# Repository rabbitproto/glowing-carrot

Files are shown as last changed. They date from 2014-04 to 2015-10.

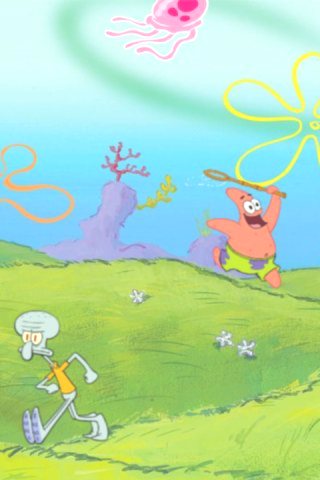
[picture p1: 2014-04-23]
demo_applications/Game Controller/Jellyfish Fields/Jellyfish_Fields/background.jpg

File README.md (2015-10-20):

Rabbit Proto Logo

Attention! Rabbit Proto is now part of Nascent Objects, we are not shipping extruders or machine anymore, but have open sourced all the latest extruder design files so the community can take over and make their own. More information on this post:

<script async src="https://static.medium.com/embed.js"></script><a class="m-story" data-collapsed="true" href="https://medium.com/@AlexandreJais/building-the-future-of-making-265a1de3fc73">Building the future of making</a>

Rabbit Proto
==============

##What##

Rabbit Proto makes plugins that easily integrate into your 3D printer, enabling it to print complex conductive traces within 3D designs.  Your 3D printer can now print interactive prototypes with capacitive and conductive features.

##Who##

Rabbit Proto has been created for designers and makers, by designers and makers - you can now speed up your prototyping and ideation process, going from computer design to interactive prototype with just one click.

##How##

Rabbit Proto is a print head add-on that easily plugs into your 3D printer, enabling it to print complex conductive traces within your 3D design. The project source code, documentation, and example designs are open source and available on GitHub. 

See Rabbit Proto in action on our website : www.rabbitproto.com

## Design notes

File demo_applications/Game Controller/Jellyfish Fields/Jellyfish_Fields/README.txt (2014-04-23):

This code won't work until you have something connected to your serial com port. So connect your Arduino, otherwise the sketch won't play.

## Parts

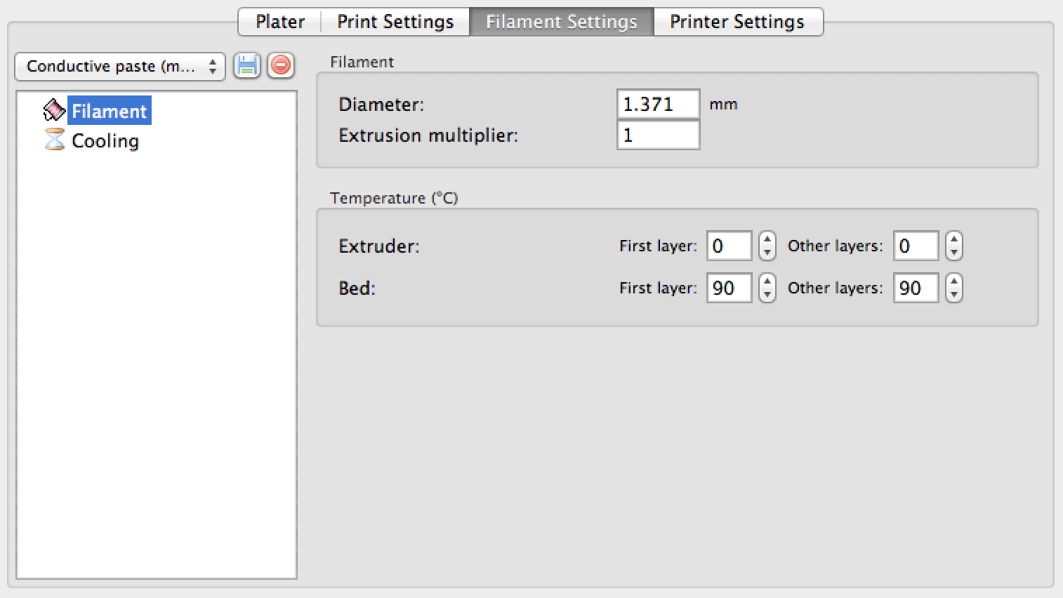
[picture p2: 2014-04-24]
Slicer Settings/Conductive Paste Material Properties.png

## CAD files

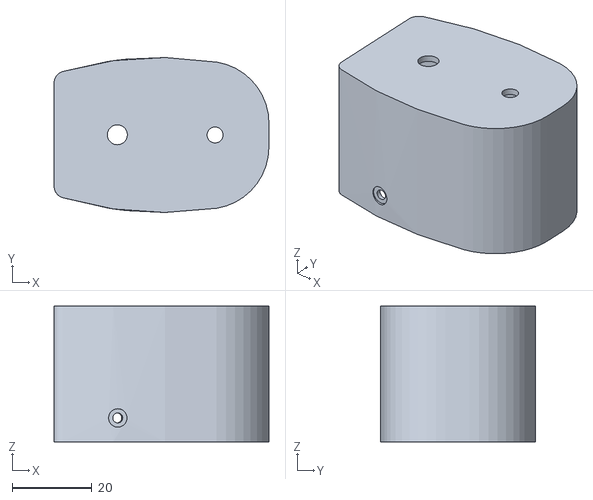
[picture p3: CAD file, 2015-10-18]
extruder_design/Dual Extruder/Extruder Assembly - Top.stl
53.8 x 38.8 x 34.0

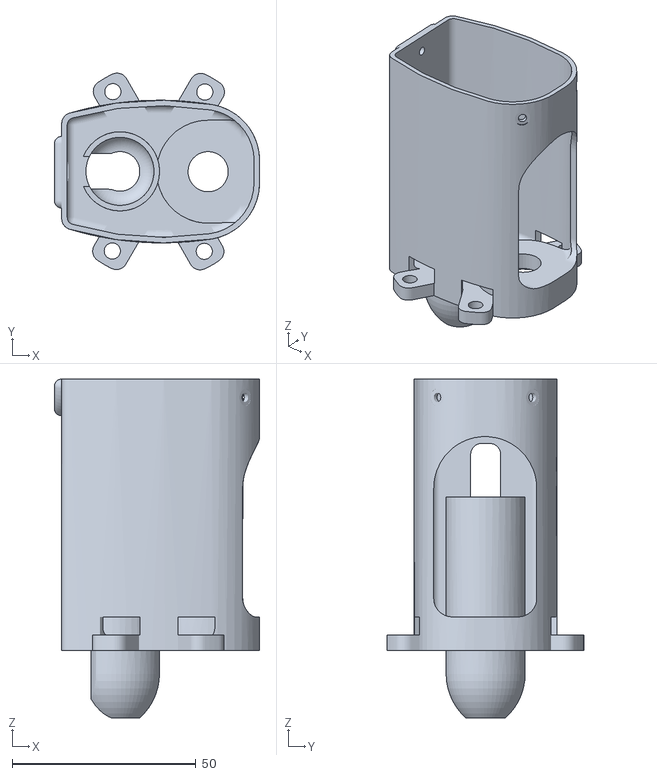
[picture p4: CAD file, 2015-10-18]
extruder_design/Dual Extruder/Extruder Assembly - Bottom.stl
55.8 x 53.5 x 92.2

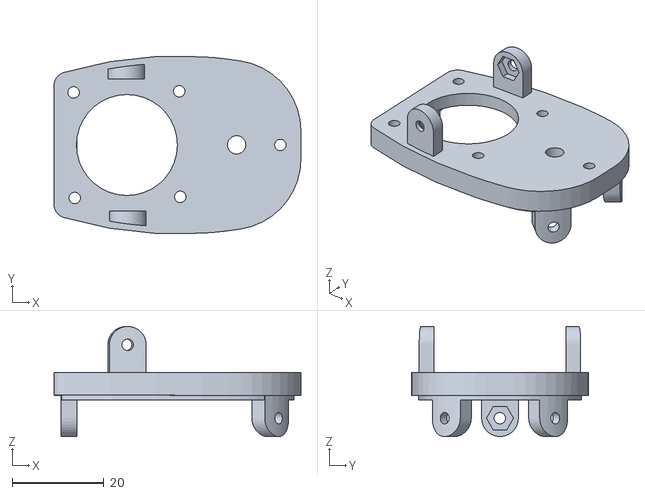
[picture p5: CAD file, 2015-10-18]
extruder_design/Dual Extruder/Extruder Assembly - Middle.stl
53.8 x 38.6 x 24.0

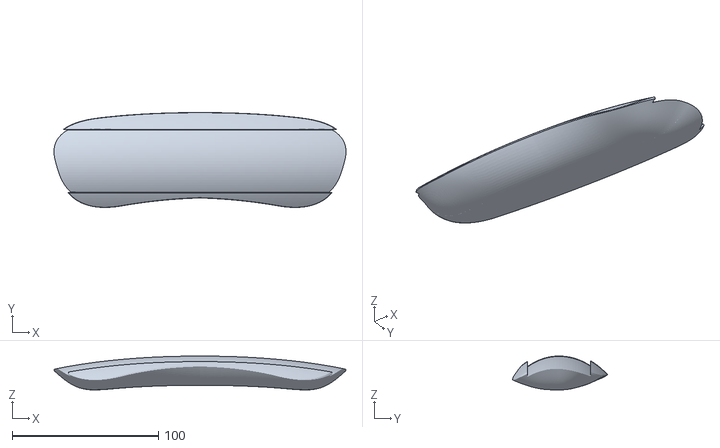
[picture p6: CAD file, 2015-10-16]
demo_applications/backrest_ll_btmcase.stl
199.6 x 64.9 x 23.2

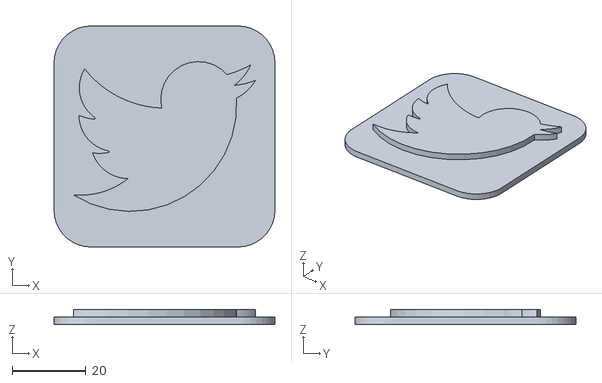
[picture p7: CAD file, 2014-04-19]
demo_applications/Conductive Twitter/Twitter3.stl
60.0 x 60.0 x 4.00

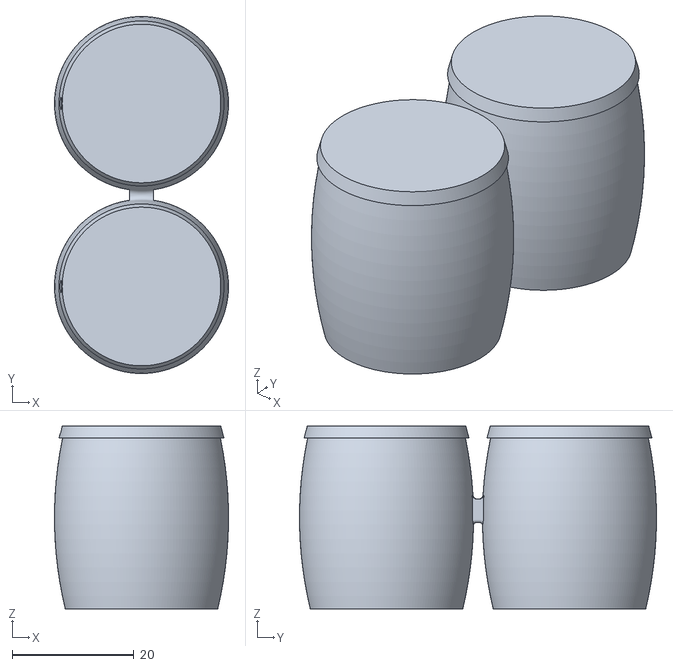
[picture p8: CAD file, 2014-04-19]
demo_applications/Congas/Congas.stl
28.5 x 58.5 x 30.0

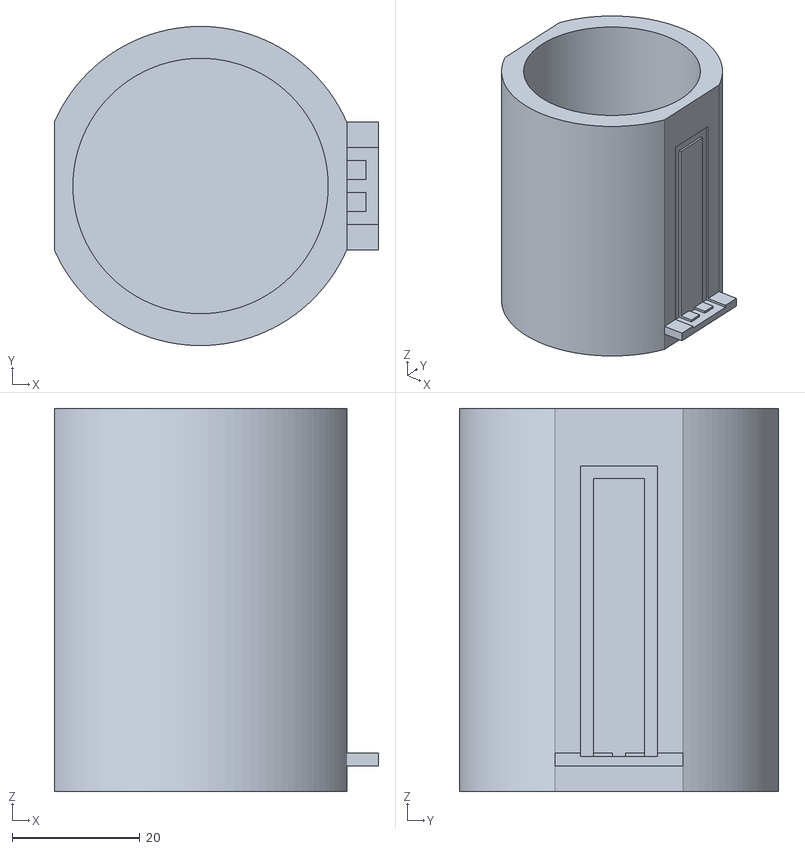
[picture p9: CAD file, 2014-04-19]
demo_applications/Cup measurement/Cup.stl
50.8 x 50.0 x 60.0

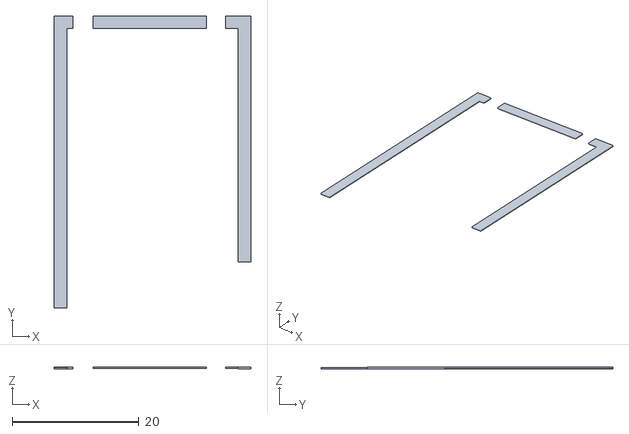
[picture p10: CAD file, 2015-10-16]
demo_applications/Cute octopus/CuteOcto(2).stl
31.0 x 46.0 x 0.301

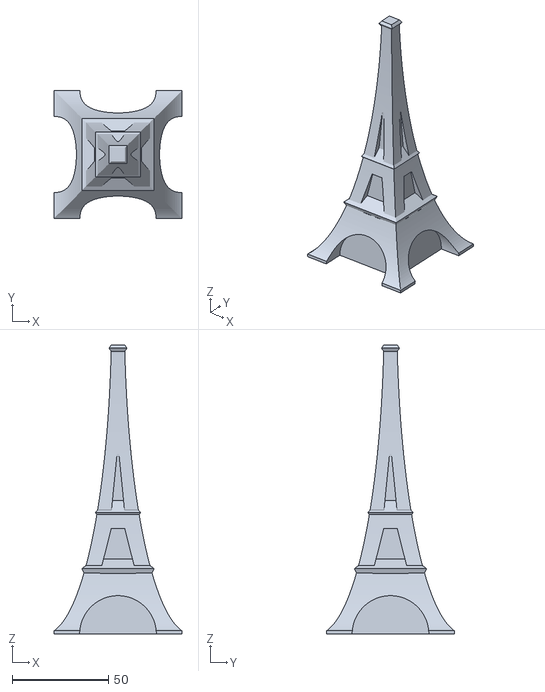
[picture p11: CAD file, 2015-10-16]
demo_applications/Eiffel Tower/Eiffel Tower.stl
66.3 x 66.3 x 150.0

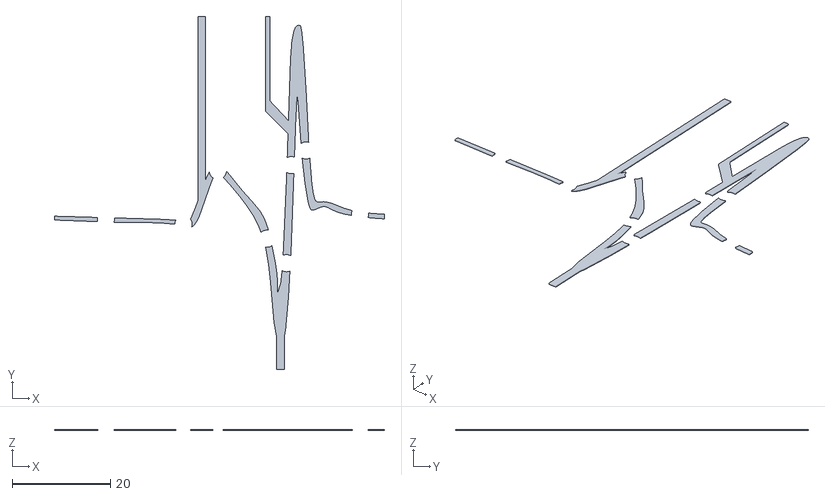
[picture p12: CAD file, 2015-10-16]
demo_applications/EKG light/EKG light V2.stl
67.3 x 72.0 x 0.25

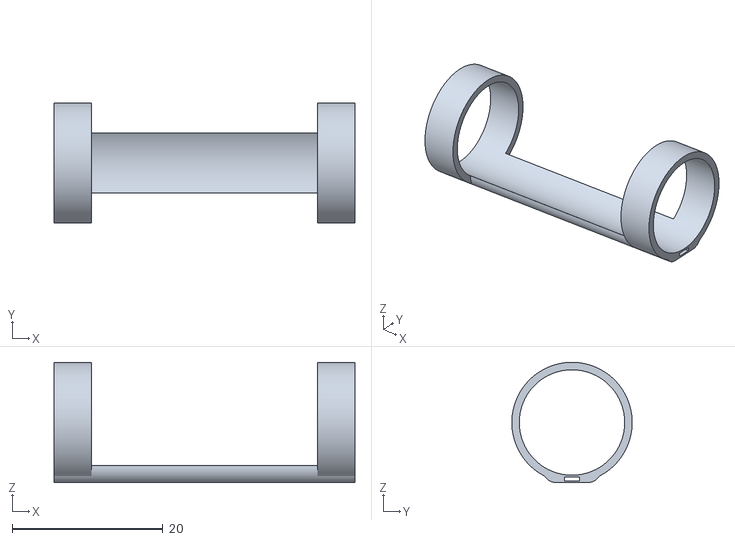
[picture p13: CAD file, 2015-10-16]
demo_applications/Finger Flex/Finger Flex.stl
40.0 x 16.0 x 16.0

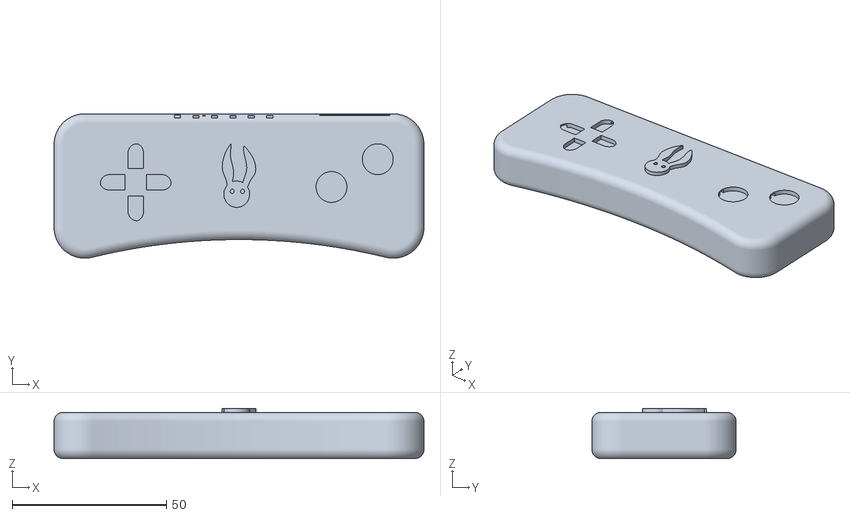
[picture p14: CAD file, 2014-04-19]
demo_applications/Game Controller/CAD/Game Controller.stl
120.0 x 46.8 x 16.3

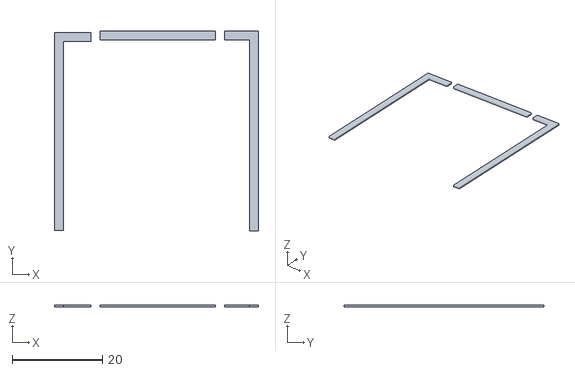
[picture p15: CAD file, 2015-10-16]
demo_applications/Glowing Rabbit 2/Glowing Rabbit 2.stl
45.2 x 44.2 x 0.5

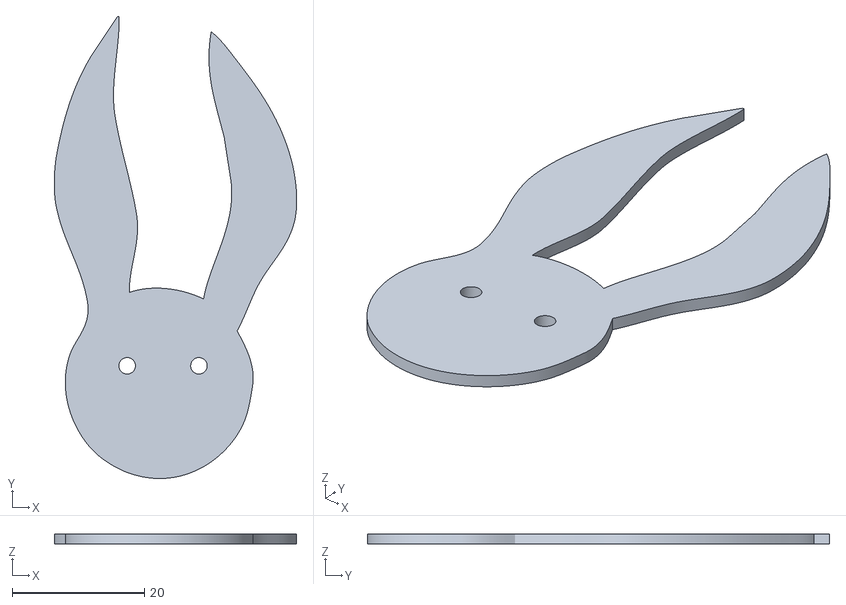
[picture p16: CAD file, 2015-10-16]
demo_applications/Glowing Rabbit 3/Glowing Rabbit.stl
36.7 x 70.0 x 1.50

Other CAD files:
demo_applications/IPhone Stylus/IPhone Stylus v3.stl
demo_applications/IPhone Stylus/Test shapes/Feather Stylus.stl
demo_applications/IPhone Stylus/Testing Session/IPhone Stylus v3.stl
demo_applications/Calibration Shapes/Design4.stl
demo_applications/Calibration Shapes/backrest_ll_topcase.stl
demo_applications/Conductive Twitter/Twitter(2).stl
demo_applications/Conductive Twitter/Twitter.amf
demo_applications/Conductive Twitter/Twitter2(2).stl
demo_applications/Conductive Twitter/Twitter3(2).stl
demo_applications/Conductive Twitter/Twitter3.amf
demo_applications/EKG light/EKG light V2(2).stl
demo_applications/EKG light/EKG light V2.amf
demo_applications/EKG light/EKG light thin(2).stl
demo_applications/EKG light/EKG light thin.amf
demo_applications/EKG light/EKG light(2).stl
demo_applications/EKG light/EKG light.amf
demo_applications/EKG light/EKG light.stl
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

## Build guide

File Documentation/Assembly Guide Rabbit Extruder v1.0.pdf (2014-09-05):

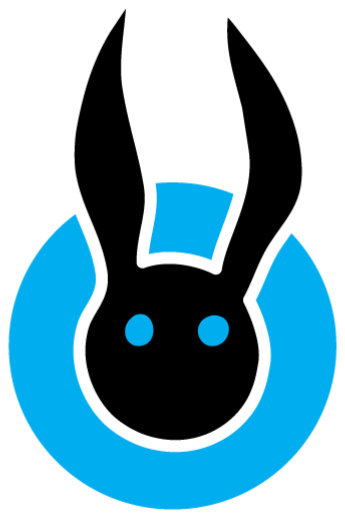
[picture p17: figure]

Please email questions or corrections to info@rabbitproto.com

# Quick guide - Rabbit Proto Extruder

V1.0 Sept 2014

## 1. Material required

Hardware
- Rep Rap 3D printer
- Rabbit Proto – Supper Rabbit PrintHead
- Copper filled silicone RTV (http://www.amazon.com/Permatex-81878-Maximum-Temperature-Silicone/dp/B0002UEOPA) (http://www.amazon.com/Permatex-81878-Maximum-Temperature-Silicone/dp/B0002UEOPA)
- Kapton tape
- Allen Wrench (Metric)
Software
- Repetier Host + Slic3r
- Arduino Software

## 2. Finalize the plastic extruder assembly

From the Rostock Max Assembly guide by SeeMeCNC

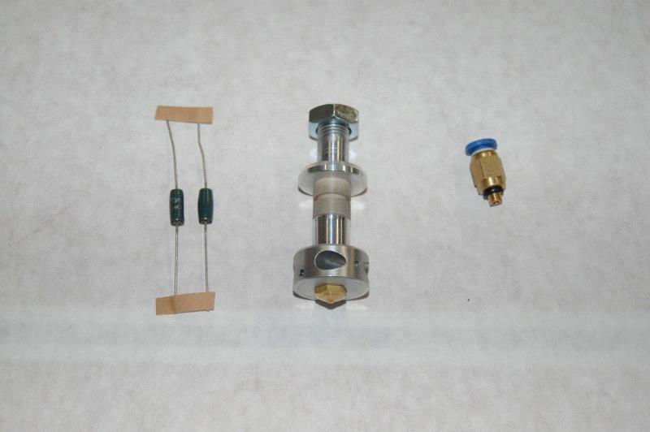
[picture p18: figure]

Hot end components.

The only tasks you need to complete involve installing the heating resistors, the thermistor and the push-fit connector.

The resistors included with the hot end (the green objects in Fig. 15-1) are too small to fit snugly into the bore holes to either side of the hot end. In order to make them bigger, you’ll need to cut a strip of aluminum foil and wrap the resistor. You want the width of the foil strip to be about 1/16” shorter than the length of the resistor body so that it can’t come into contact with the leads on either end of the resistor.

Note that in order to shield the resistor leads from accidental shorts, you should wrap the leads in Kapton tape.

Once you've got the resistors installed in the hot end with a snug fit, cover each end with RTV to glue them into place. We use RTV here because if you have a resistor failure, it can be removed easily, but is very resistant to high temperatures.

Before the RTV cures, install a 3/4” length of PTFE tubing on each of the resistor leads as shown below.

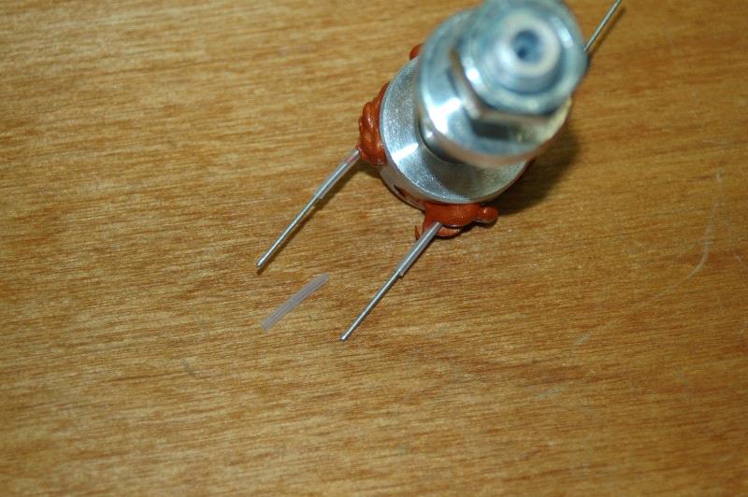
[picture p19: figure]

Insulating the hot end resistor leads.

Once the RTV cures, carefully twist the resistor leads together as shown below. Use a pair of needle nose pliers to help you get a good, tight twist.

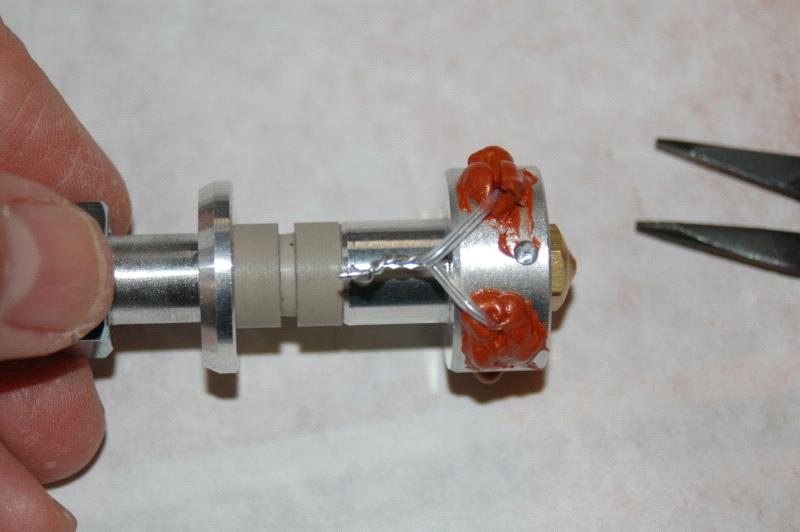
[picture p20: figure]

Resistor leads twisted together

When you're done twisting the leads together, clip about 1/16” to 1/8” off each end to clean up the ends a bit. A crimp connector will go on them and you want the best fit you can get.

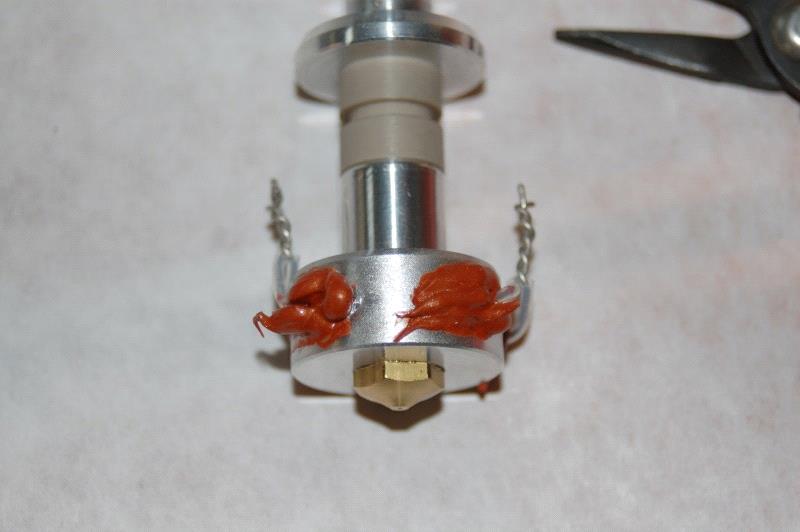
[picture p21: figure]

Resistor leads ready to crimp.

Because of the temperatures reached by the hot end, we can't use solder to attach the power wires to the resistors. Use crimps marked “22-16”. Crimp one connector to each twisted pair of resistor leads as shown below.

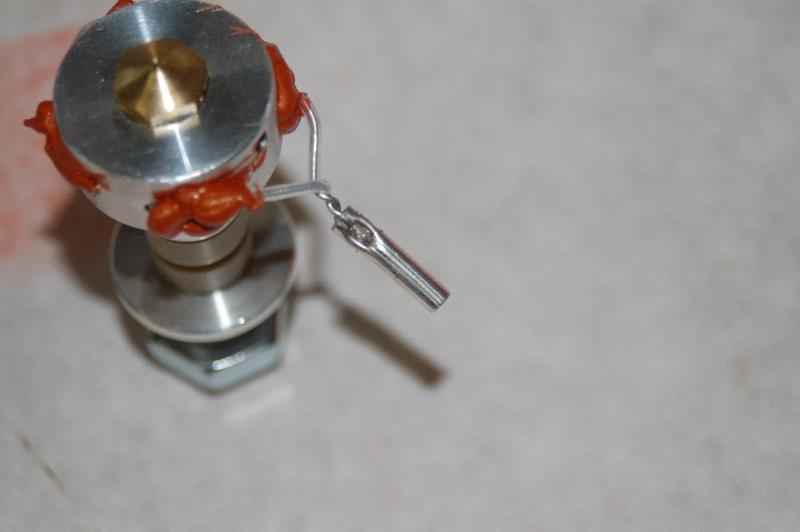
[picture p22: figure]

Crimp on connector in place.

Note that you only want to crimp it in one place.

The lower portion of the hot end is threaded on to a PEEK barrel that acts like a thermal break. In order to keep repeated heating and cooling cycles from loosening the hot end from the PEEK, wrap the seam with a short length of Kapton tape as shown below.

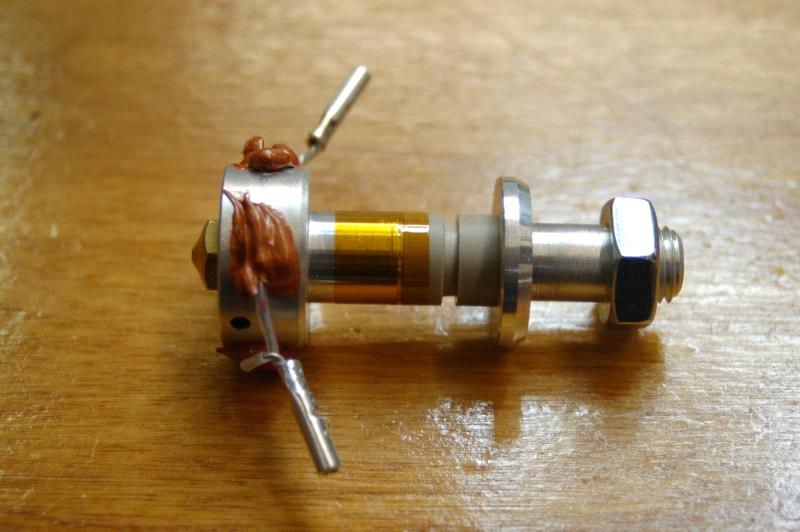
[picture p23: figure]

Kapton wrap on the PEEK barrel.

I prefer to use a quick disconnect connector on my hot-end and I strongly suggest you do the same. In Section 1 I list two different types – the Deans and XT-60 connectors. My preference is the XT-60, but if you've got Deans on hand, they're well suited to the task. I won't show how to attach them – it should be pretty obvious and if not, there's always Google. :) I'm going with the assumption that you like to be able to change out hot-ends and have installed the connectors of your choice.

Attach a 3” or so length of 16ga wire (one black, one red) to the crimped connectors, and wrap them in Kapton tape to insulate them.

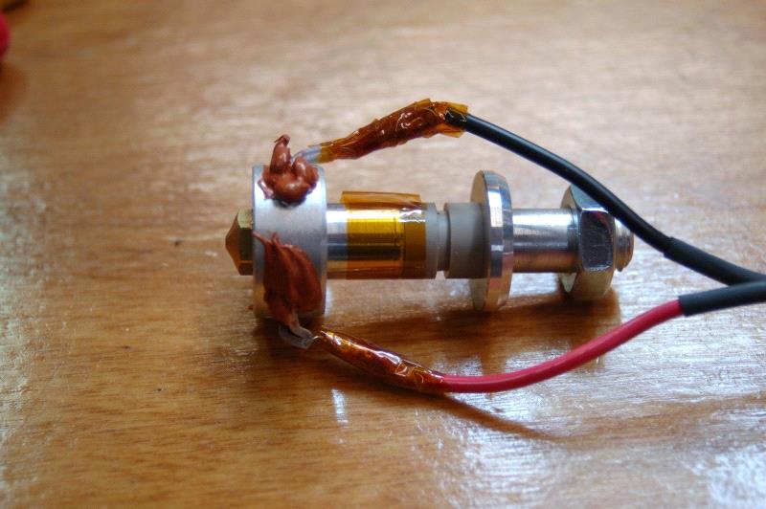
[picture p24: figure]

Attaching the power leads to the hot end.

Now you need to install the thermistor into the hot end. A thermistor is a tiny temperature sensing device that changes resistance as the temperature around it changes. I cannot stress this enough it's a very delicate component! Please handle it very carefully! The glass bead is fragile and the wire can be brittle if soldered and moved too much.

First, cut two 1” lengths of the included PTFE tubing and slide them over the thermistor leads as shown:

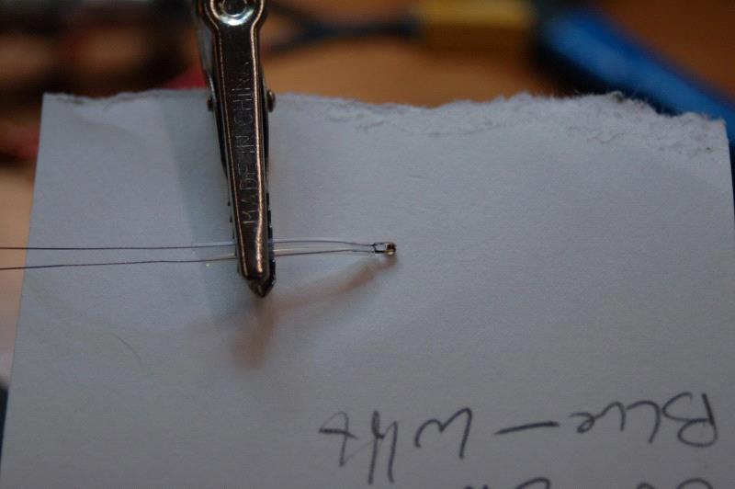
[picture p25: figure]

Insulating the thermistor leads.

Just like the resistor wiring, I recommend you use a quick disconnect connector. For the thermistor, I recommend using a JST connector. You can cut a 2” long section from the wiring supplied for doing the stepper motor extension for this purpose. Thermistors have no polarity, so it doesn't matter how you attach the JST connectors.

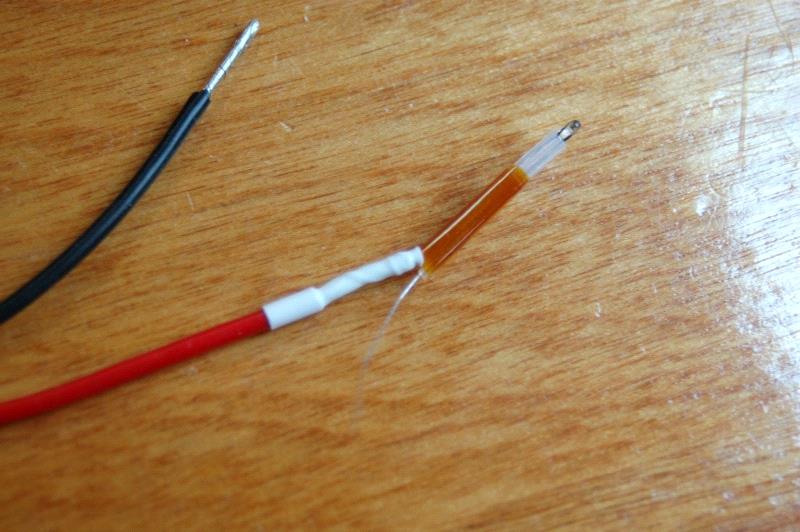
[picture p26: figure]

Attaching leads to the thermistor.

Now you can solder your leads to the thermistor. I recommend covering the solder joint with heat shrink tubing. The thermistor wires won't get hot enough to affect it. You'll also see that I taped the leads together with Kapton tape. This is done to give it a bit more protection.

Be careful when you're soldering this up. The thermistor leads are very brittle and can break easily once soldered.

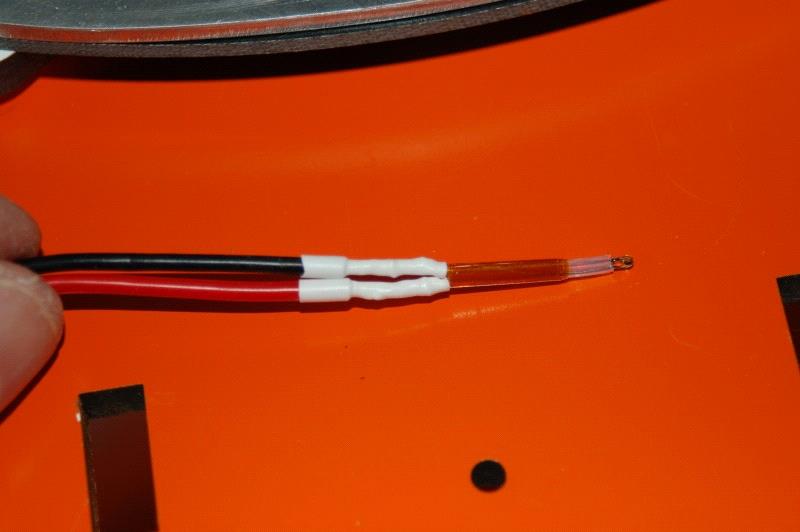
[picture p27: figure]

Thermistor ready to install.

Once you've got the leads added, I strongly suggest that you use Kapton tape or more heat shrink to bind the two leads together at the joint – this will help prevent flex that could cause the thermistor lead solder joint to fail. The thermistor is installed in the hot end at the location shown in Fig. 15-11.

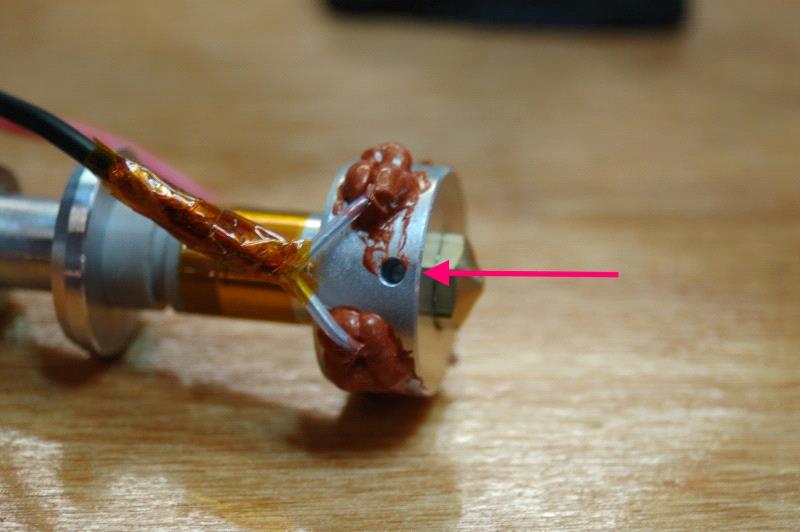
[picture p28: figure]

Thermistor installation location.

In order to “glue” the thermistor into place, you'll need to coat the sides of the thermistor bead with a small amount of RTV as shown in Fig. 15-12.

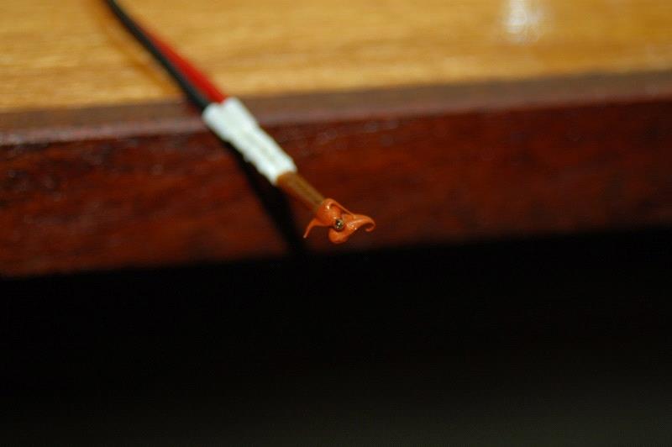
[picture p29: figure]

RTV applied to the thermistor sides.

The idea here is to leave the tip of the glass bead exposed. This will allow it to come into unobstructed contact with the thermistor port on the hot end.

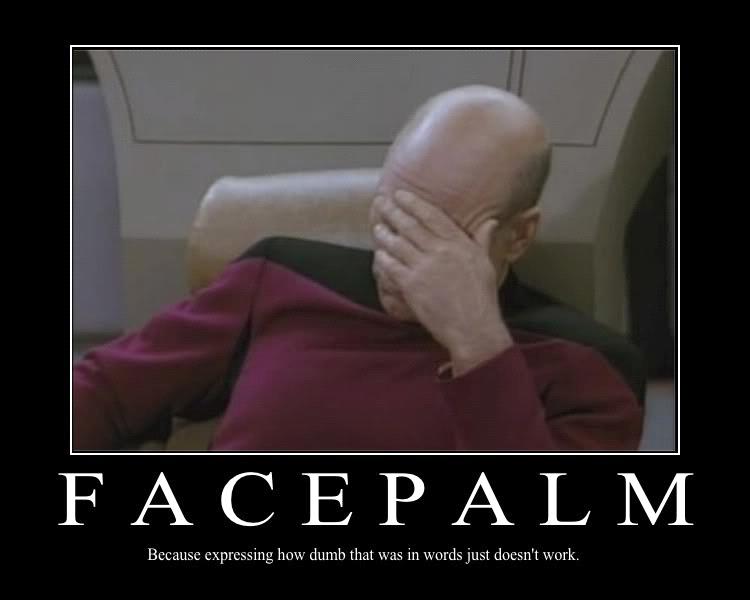
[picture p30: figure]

D'OH!

Wait, you just broke the wires on your thermistor, didn't you? Oh. You didn't? Well I just did.

So instead of doing the technical writing equivalent of sweeping the bits of broken ceramic under the couch with your foot while smiling and telling your mother you have no idea where her prize vase is, I'm going to show you photos of the thermistor as I actually installed it.

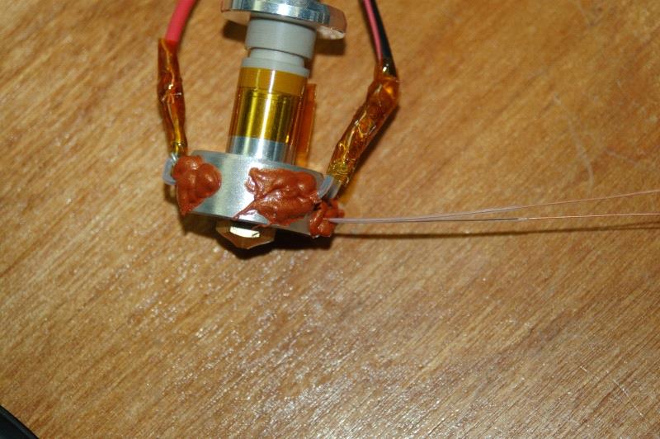
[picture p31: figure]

Magically repaired (and slightly different) thermistor installed in the hot end.

Please give the RTV time to fully cure before you move on to the next steps.

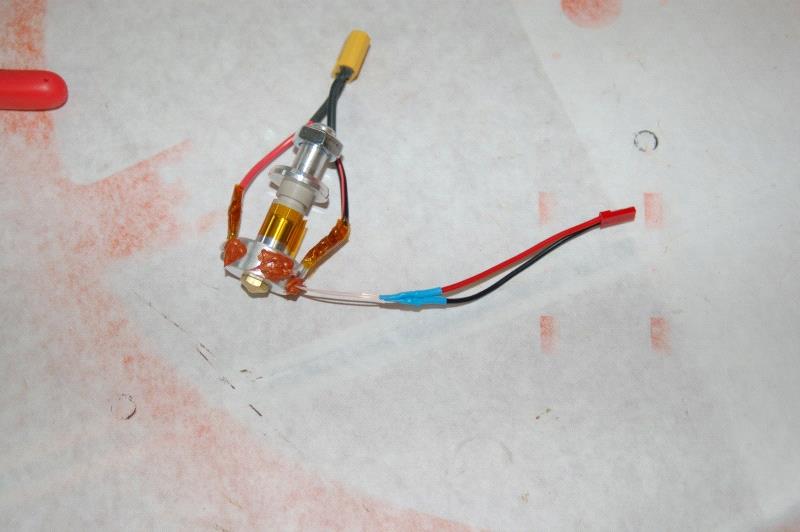
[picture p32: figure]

Magic thermistor with JST connector in place.

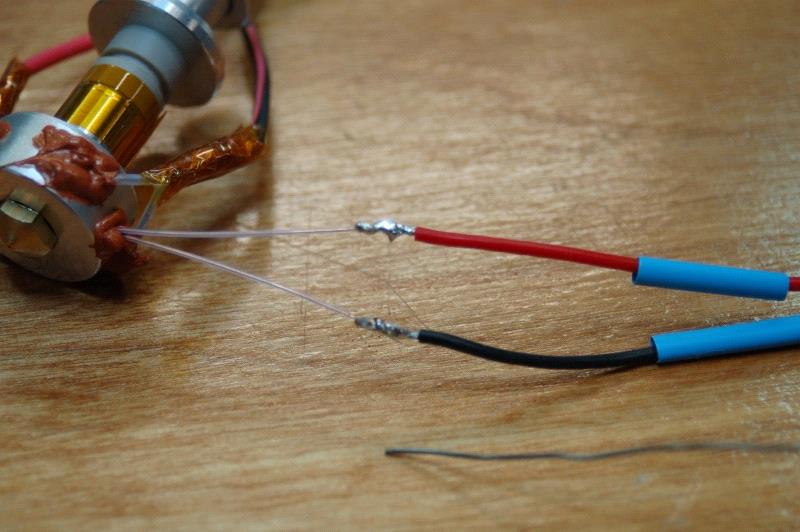
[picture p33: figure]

Magic thermistor getting JST connector.

## 3. Attach the extruder to your 3D printer

a. Design and print an adapter (if needed)

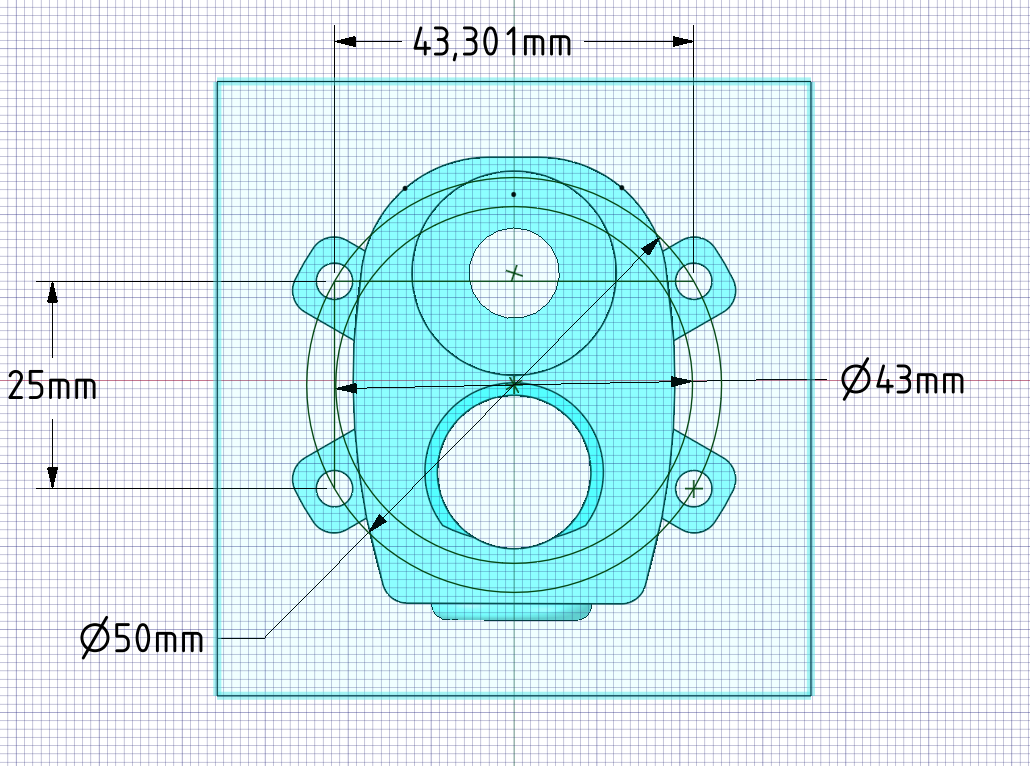
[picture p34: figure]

Rabbit Proto’s footprint.
If you own a Mendel Prusa or a Rostock, there is a high chance you will be able to attach the RP extruder directly to your machine. Otherwise you should be able to print a carriage adapter that can hold the extruder.
b. Optional – Bowden extruder assembly
If you don’t have a Bowden-compatible extrusion system, we have included an Ezstruder system from SeeMeCnc (http://seemecnc.com/products/ezstruder-cold-end-kit). Assembly should be straightforward but you’ll find documentation on their website (or look at this video and ignore the hot-end assembly part). https://www.youtube.com/watch?v=2bmbvPiY7qM#t=191
c. Attach to the printer or your homemade adapter using screw and self-locking nuts preferably
d. Connect the second extruder stepper motor on your board. If your printer is compatible with dual extrusion, you should have an available port for the conductive paste extruder stepper motor.

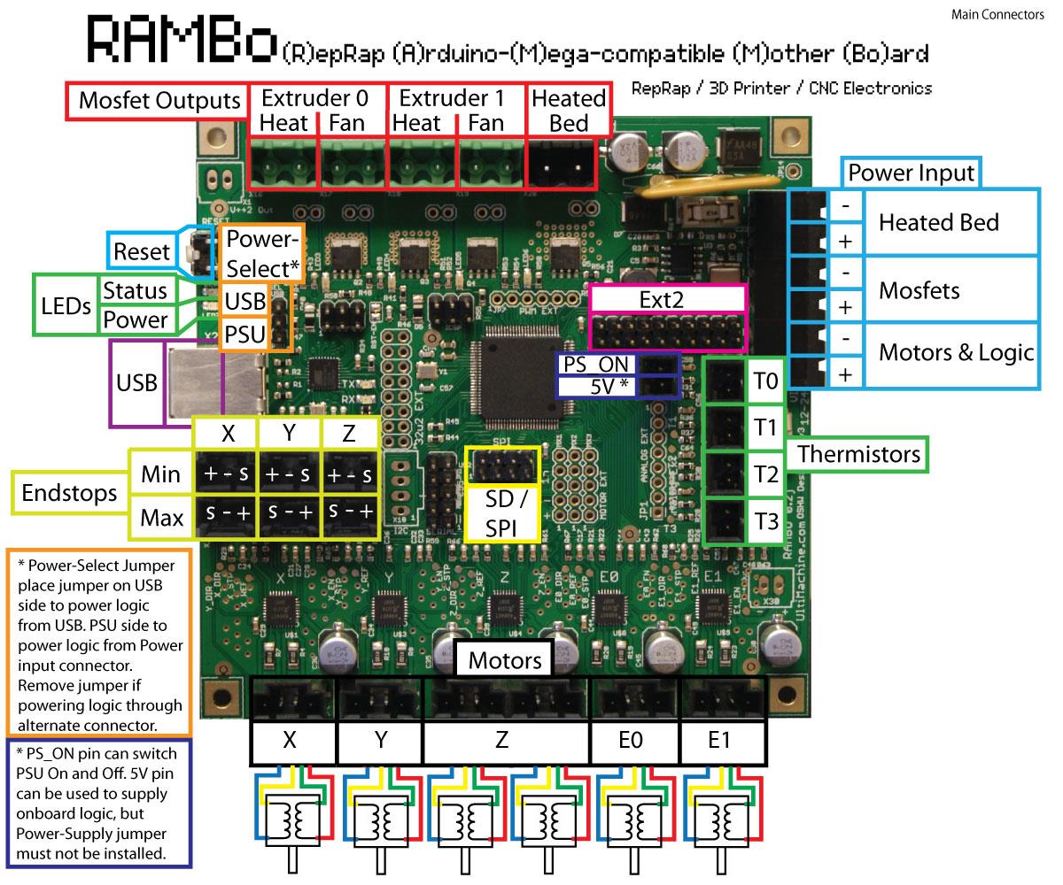
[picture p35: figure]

On the Rambo Board use the port noted E1.

## 4. Modify your printer’s firmware

In order to be able to use your second extruder, you need to modify the configuration file of the firmware of your machine. The amount of modification is in general extremely small especially if the settings of your printer can be modified with the EEPROM. You can find a copy of a modified Repetier Firmware for Rostock Max on our github at https://github.com/rabbitproto/glowing-carrot/. The three most important steps to take:
- Set up two extruders
- Allow cold extrusion (so that your second extruder can work even without any thermistor checking the temperature).
- Tune up the number of steps per mm for the second extruder (1100 steps/mm).
- If you end-up using the Ez-struder, you will also need to change the number of steps per mm.

## 5. Configuration in Repetier Host/Slic3r

Tuned Slic3r parameters:
Parameters | Values
Layer Height | 0.2mm
First Layer Height | 0.35mm
Minimum Perimeters | 2
Fill Density | 1
Fill Pattern | Rectilinear
Top/Bottom Fill Pattern | Rectilinear
Infill Every # Layers | 1
Solid Infill Every # Layers | 1
Fill Angle | 0
Perimeter Speed | 60mm/s
Small Perimeter Speed | 10mm/s
External Perimeter Speed | 70%
Infill Speed | 60mm/s
Solid Infill Speed | 60mm/s
Top Solid Infill Speed | 60mm/s
Support Material Speed | 60mm/s
Bridges Speed | 60mm/s
Gap Speed | 60mm/s
Non Printing Speed | 130mm/s
First Layer Speed | 30%
Skirt Loops | 2
Skirt Distance from Objects | 6mm
Skirt Height | 1 Layer Height
Support Material Pattern | Rectilinear
Support Material Pattern Spacing | 2.5mm
Support Material Pattern Angle | 0
Default Extrusion Width | 0.4mm
First Layer Extrusion Width | 300%
Plastic Filament Diameter | 1.75 mm (please check for your own
| filament)
Plastic Extrusion Multiplier | 1
Plastic Extrusion Nozzle Temperature | 230°C
Plastic Extrusion Print-bed Temperature | 55
Syringe Filament Diameter | 7.358491
Syringe Extrusion Multiplier | 4
Syringe Extrusion Nozzle Temperature | 0
Syringe Extrusion Print-bed Temperature | 0
Print-bed Size | Depending on your printer
Printer Center | Depending on your printer
Number of Extruders | 2

Z-offset | 0
Plastic Extruder Retraction Length | 0.5mm
Plastic Extruder Retraction Speed | 6mm/s
Tool Change Retraction Length for Plastics | 0.5mm
Syringe Extruder X-offset | 1.1mm
Syringe Extruder Y-offset | -24.6mm
Syringe Extruder Retraction Length | 0.001mm
Syringe Extruder Retraction Speed | 1mm/s
Extra Extrusion on Restart for Syringe | 0.01mm
Tool Change Retraction Length for Syringe | 0

Please fine tune the offsets and the extrusion multipliers as there could be some fine modifications needed after a few prints.

## 6. Generating a CAD file

In order to generate a proper CAD file for printing with the Rabbit Extruder, you can use any standard CAD solution as long as you are able to generate multiple components that will be outputted as STL files. One will contain the plastic, the other one the conductive traces. You will want to have wells pre-formed into your plastic parts to hold the conductive traces. You can also add cavities for holding electronic components that you can pick and place during or after the print:

General requirements for design:
Features | Dimensions
Conductive traces | for cross-section 1.20x0.4mm
Plastic wells to contain conductive
traces

for cross-section 2.0x0.6mm

Cavities to hold SMT LEDs | 4.3x1.2x1.2mm
Cavities to hold regular resistors | 7.6x2.8x3.5mm
Cavities to hold 3 parallel male pin
headers

9.5x3.5x3mm

Cavities to hold 3 parallel female pin
headers

9.2x3.2x8.9mm

Cavities to hold 2025 button batteries Dia: 21mm thickness 5.8mm

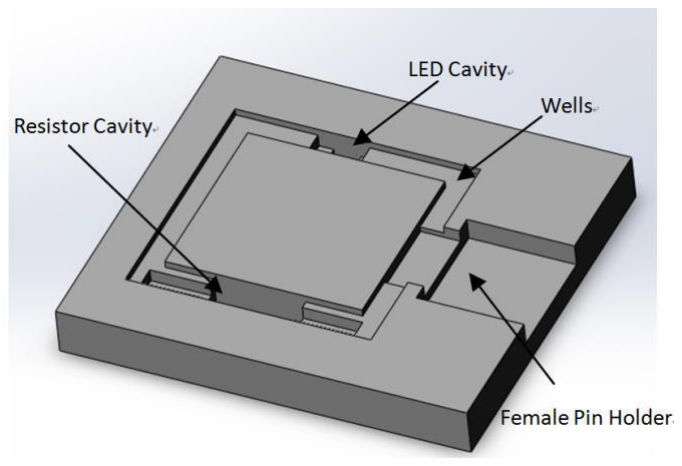
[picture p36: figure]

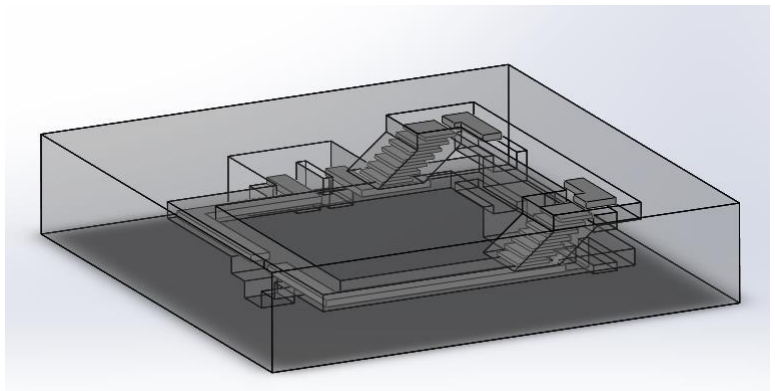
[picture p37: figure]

## 7. Printing using Repetier Host

Slic3r can output gcode for a multi-material printer, which can then be read inside repetier host. You can find more details on how to generate proper gcode at http://manual.slic3r.org/expert-mode/multiple-extruders.

## 8. Uploading your designs

Please share your designs with the Rabbit Proto community! A current repository of designs is available on our github, at https://github.com/rabbitproto/glowing-carrot/tree/master/demo_applications, (https://github.com/rabbitproto/glowing-carrot/tree/master/demo_applications) and our twitter handle is @rabbitproto.

Please email questions or corrections to info@rabbitproto.com

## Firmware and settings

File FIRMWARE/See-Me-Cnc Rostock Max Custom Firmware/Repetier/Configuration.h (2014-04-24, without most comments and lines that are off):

#define CONFIGURATION_H
#define NUM_EXTRUDER 2
#define MOTHERBOARD 301
#include "pins.h"
#define DRIVE_SYSTEM 3
#if DRIVE_SYSTEM==3
    #define DELTA_DRIVE_TYPE 0
    #if DELTA_DRIVE_TYPE == 0
      #define BELT_PITCH 2
      #define PULLEY_TEETH 20
      #define PULLEY_CIRCUMFERENCE (BELT_PITCH * PULLEY_TEETH)
    #elif DELTA_DRIVE_TYPE == 1
      #define PULLEY_DIAMETER 10
      #define PULLEY_CIRCUMFERENCE (PULLEY_DIAMETER * 3.1415927)
    #endif
    #define STEPS_PER_ROTATION 200
    #define MICRO_STEPS 16
    #define MAX_DELTA_SEGMENTS_PER_LINE 30
    #define AXIS_STEPS_PER_MM ((float)(MICRO_STEPS * STEPS_PER_ROTATION) / PULLEY_CIRCUMFERENCE)
    #define XAXIS_STEPS_PER_MM AXIS_STEPS_PER_MM
    #define YAXIS_STEPS_PER_MM AXIS_STEPS_PER_MM
    #define ZAXIS_STEPS_PER_MM AXIS_STEPS_PER_MM
#else
    #define XAXIS_STEPS_PER_MM 80.000
    #define YAXIS_STEPS_PER_MM 80.000
    #define ZAXIS_STEPS_PER_MM 80.000
#endif
#define EXTRUDER_FAN_COOL_TEMP 40
#define EXT0_X_OFFSET 0
#define EXT0_Y_OFFSET 0
#define EXT0_STEPS_PER_MM 92.000 //steves extruder    set to 92 for ezstruder
#define EXT0_TEMPSENSOR_TYPE 8
#define EXT0_TEMPSENSOR_PIN TEMP_0_PIN
#define EXT0_HEATER_PIN HEATER_0_PIN
#define EXT0_STEP_PIN E0_STEP_PIN
#define EXT0_DIR_PIN E0_DIR_PIN
#define EXT0_INVERSE true
#define EXT0_ENABLE_PIN E0_ENABLE_PIN
#define EXT0_ENABLE_ON false
#define EXT0_MAX_FEEDRATE 40
#define EXT0_MAX_START_FEEDRATE 10
#define EXT0_MAX_ACCELERATION 3500
#define EXT0_HEAT_MANAGER 1
#define EXT0_WATCHPERIOD 1
#define EXT0_PID_INTEGRAL_DRIVE_MAX 205
#define EXT0_PID_INTEGRAL_DRIVE_MIN 60
#define EXT0_PID_P   11.63
#define EXT0_PID_I   0.43
#define EXT0_PID_D 78.65
#define EXT0_PID_MAX 255
#define EXT0_ADVANCE_K 0.0f
#define EXT0_ADVANCE_L 0.0f
#define EXT0_WAIT_RETRACT_TEMP 		150
#define EXT0_WAIT_RETRACT_UNITS 	0
#define EXT0_SELECT_COMMANDS "M120 S5 P5\nM117 Extruder 1"
#define EXT0_DESELECT_COMMANDS ""
#define EXT0_EXTRUDER_COOLER_PIN 7
#define EXT0_EXTRUDER_COOLER_SPEED 255
#define EXT1_X_OFFSET 0
#define EXT1_Y_OFFSET 0
#define EXT1_STEPS_PER_MM 373
#define EXT1_TEMPSENSOR_TYPE 0
#define EXT1_TEMPSENSOR_PIN TEMP_2_PIN
#define EXT1_HEATER_PIN HEATER_2_PIN
#define EXT1_STEP_PIN E1_STEP_PIN
#define EXT1_DIR_PIN E1_DIR_PIN
#define EXT1_INVERSE false
#define EXT1_ENABLE_PIN E1_ENABLE_PIN
#define EXT1_ENABLE_ON false
#define EXT1_MAX_FEEDRATE 25
#define EXT1_MAX_START_FEEDRATE 12
#define EXT1_MAX_ACCELERATION 10000
#define EXT1_HEAT_MANAGER 1
#define EXT1_WATCHPERIOD 1
#define EXT1_PID_INTEGRAL_DRIVE_MAX 130
#define EXT1_PID_INTEGRAL_DRIVE_MIN 60
#define EXT1_PID_P   24
#define EXT1_PID_I   0.88
#define EXT1_PID_D 200
#define EXT1_PID_MAX 255
#define EXT1_ADVANCE_K 0.0f
#define EXT1_ADVANCE_L 0.0f
#define EXT1_WAIT_RETRACT_TEMP 	150
#define EXT1_WAIT_RETRACT_UNITS	40
#define EXT1_SELECT_COMMANDS "M120 S5 P15\nM117 Extruder 2"
#define EXT1_DESELECT_COMMANDS ""
#define EXT1_EXTRUDER_COOLER_PIN -1
#define EXT1_EXTRUDER_COOLER_SPEED 255
#define RETRACT_DURING_HEATUP true
#define PID_CONTROL_RANGE 15
#define SKIP_M109_IF_WITHIN 2
#define SCALE_PID_TO_MAX 0
#define NUM_TEMPS_USERTHERMISTOR0 28
#define USER_THERMISTORTABLE0  {\
  {1*4,864*8},{21*4,300*8},{25*4,290*8},{29*4,280*8},{33*4,270*8},{39*4,260*8},{46*4,250*8},{54*4,240*8},{64*4,230*8},{75*4,220*8},\
  {90*4,210*8},{107*4,200*8},{128*4,190*8},{154*4,180*8},{184*4,170*8},{221*4,160*8},{265*4,150*8},{316*4,140*8},{375*4,130*8},\
  {441*4,120*8},{513*4,110*8},{588*4,100*8},{734*4,80*8},{856*4,60*8},{938*4,40*8},{986*4,20*8},{1008*4,0*8},{1018*4,-20*8}	}
#define NUM_TEMPS_USERTHERMISTOR1 0
#define USER_THERMISTORTABLE1  {}
#define NUM_TEMPS_USERTHERMISTOR2 0
#define USER_THERMISTORTABLE2  {}
#define GENERIC_THERM1_R0 100000
#define GENERIC_THERM1_T0 25
#define GENERIC_THERM1_BETA 4450
#define GENERIC_THERM1_MIN_TEMP -20
#define GENERIC_THERM1_MAX_TEMP 300
#define GENERIC_THERM1_R1 0
#define GENERIC_THERM1_R2 4700
#define GENERIC_THERM2_R0 1042.7
#define GENERIC_THERM2_T0 170
#define GENERIC_THERM2_BETA 4036
#define GENERIC_THERM2_MIN_TEMP -20
#define GENERIC_THERM2_MAX_TEMP 300
#define GENERIC_THERM2_R1 0
#define GENERIC_THERM2_R2 4700
#define GENERIC_THERM3_R0 1042.7
#define GENERIC_THERM3_T0 170
#define GENERIC_THERM3_BETA 4036
#define GENERIC_THERM3_MIN_TEMP -20
#define GENERIC_THERM3_MAX_TEMP 300
#define GENERIC_THERM3_R1 0
#define GENERIC_THERM3_R2 4700
#define GENERIC_THERM_VREF 5
#define GENERIC_THERM_NUM_ENTRIES 28
#define HAVE_HEATED_BED true
#define HEATED_BED_MAX_TEMP 115
#define SKIP_M190_IF_WITHIN 5
#define HEATED_BED_SENSOR_TYPE 8
#define HEATED_BED_SENSOR_PIN TEMP_BED_PIN  //CHANGE FROM TEMP_1_PIN TO TEMP_BED_PIN FOR RAMBo
#define HEATED_BED_HEATER_PIN HEATER_BED_PIN   //CHANGE FROM HEATER_1_PIN TO TEMP_BED_PIN FOR RAMBo
#define HEATED_BED_SET_INTERVAL 5000
#define HEATED_BED_HEAT_MANAGER 1
#define HEATED_BED_PID_INTEGRAL_DRIVE_MAX 255
#define HEATED_BED_PID_INTEGRAL_DRIVE_MIN 80
#define HEATED_BED_PID_PGAIN   15.0
#define HEATED_BED_PID_IGAIN   0.9
#define HEATED_BED_PID_DGAIN 40.0
#define HEATED_BED_PID_MAX 230
#define TEMP_PID true
#define MINTEMP 5
#define MAXTEMP 250
#define MIN_DEFECT_TEMPERATURE -10
#define MAX_DEFECT_TEMPERATURE 300
#define ANALOG_REF ANALOG_REF_AVCC
#define ENDSTOP_PULLUP_X_MIN true
#define ENDSTOP_PULLUP_Y_MIN true
#define ENDSTOP_PULLUP_Z_MIN true
#define ENDSTOP_PULLUP_X_MAX true
#define ENDSTOP_PULLUP_Y_MAX true
#define ENDSTOP_PULLUP_Z_MAX true
#define ENDSTOP_X_MIN_INVERTING true
#define ENDSTOP_Y_MIN_INVERTING true
#define ENDSTOP_Z_MIN_INVERTING true
#define ENDSTOP_X_MAX_INVERTING false
#define ENDSTOP_Y_MAX_INVERTING false
#define ENDSTOP_Z_MAX_INVERTING false
#define MIN_HARDWARE_ENDSTOP_X false
#define MIN_HARDWARE_ENDSTOP_Y false
#define MIN_HARDWARE_ENDSTOP_Z false
#define MAX_HARDWARE_ENDSTOP_X true
#define MAX_HARDWARE_ENDSTOP_Y true
#define MAX_HARDWARE_ENDSTOP_Z true
#define X_ENABLE_ON 0
#define Y_ENABLE_ON 0
#define Z_ENABLE_ON 0
#define DISABLE_X false
#define DISABLE_Y false
#define DISABLE_Z false
#define DISABLE_E false
#define INVERT_X_DIR false
#define INVERT_Y_DIR false
#define INVERT_Z_DIR false
#define X_HOME_DIR 1
#define Y_HOME_DIR 1
#define Z_HOME_DIR 1
#define max_software_endstop_r true
#define min_software_endstop_x false
#define min_software_endstop_y false
#define min_software_endstop_z false
#define max_software_endstop_x true
#define max_software_endstop_y true
#define max_software_endstop_z true
#define ENDSTOP_X_BACK_MOVE 10
#define ENDSTOP_Y_BACK_MOVE 10
#define ENDSTOP_Z_BACK_MOVE 10
#define ENDSTOP_X_RETEST_REDUCTION_FACTOR 4
#define ENDSTOP_Y_RETEST_REDUCTION_FACTOR 4
#define ENDSTOP_Z_RETEST_REDUCTION_FACTOR 4
#define ENDSTOP_X_BACK_ON_HOME 5
#define ENDSTOP_Y_BACK_ON_HOME 5
#define ENDSTOP_Z_BACK_ON_HOME 5
#define ALWAYS_CHECK_ENDSTOPS true
#define X_MAX_LENGTH 360.8
#define Y_MAX_LENGTH 360.8
#define Z_MAX_LENGTH 360.8
#define X_MIN_POS 0
#define Y_MIN_POS 0
#define Z_MIN_POS 0
#define MICROSTEP_MODES {16,16,16,16,16} // [1,2,4,8,16]
#define MOTOR_CURRENT {175,175,175,225,100} // Values 0-255 (RAMBO 135 = ~0.75A, 185 = ~1A)
#if DRIVE_SYSTEM==3
#define DELTA_DIAGONAL_ROD 269.0 // mm
#define DELTA_SEGMENTS_PER_SECOND_PRINT 200 // Move accurate setting for print moves
#define DELTA_SEGMENTS_PER_SECOND_MOVE 70 // Less accurate setting for other moves
#define END_EFFECTOR_HORIZONTAL_OFFSET 33
#define CARRIAGE_HORIZONTAL_OFFSET 35
#define PRINTER_RADIUS 198.25
#define DELTA_RADIUS (PRINTER_RADIUS-END_EFFECTOR_HORIZONTAL_OFFSET-CARRIAGE_HORIZONTAL_OFFSET)
#define STEP_COUNTER
#define SOFTWARE_LEVELING
#endif
#define STEPPER_INACTIVE_TIME 6000
#define MAX_INACTIVE_TIME 9000
#define MAX_FEEDRATE_X 200
#define MAX_FEEDRATE_Y 200
#define MAX_FEEDRATE_Z 200
#define HOMING_FEEDRATE_X 80
#define HOMING_FEEDRATE_Y 80
#define HOMING_FEEDRATE_Z 80
#define ENABLE_BACKLASH_COMPENSATION false
#define Z_BACKLASH 0
#define X_BACKLASH 0
#define Y_BACKLASH 0
#define RAMP_ACCELERATION 1
#define STEPPER_HIGH_DELAY 0
#define STEP_DOUBLER_FREQUENCY 12000
#define ALLOW_QUADSTEPPING true
#define DOUBLE_STEP_DELAY 1 // time in us
#define MAX_HALFSTEP_INTERVAL 1999
#define MAX_ACCELERATION_UNITS_PER_SQ_SECOND_X 3500
#define MAX_ACCELERATION_UNITS_PER_SQ_SECOND_Y 3500
#define MAX_ACCELERATION_UNITS_PER_SQ_SECOND_Z 3500
#define MAX_TRAVEL_ACCELERATION_UNITS_PER_SQ_SECOND_X 3500
#define MAX_TRAVEL_ACCELERATION_UNITS_PER_SQ_SECOND_Y 3500
#define MAX_TRAVEL_ACCELERATION_UNITS_PER_SQ_SECOND_Z 3500
#define MAX_JERK 20.0
#define MAX_ZJERK 20.0
#define MOVE_CACHE_SIZE 16
#define MOVE_CACHE_LOW 10
#define LOW_TICKS_PER_MOVE 250000
#define TIMER0_PRESCALE 64
#define MIN_EXTRUDER_TEMP 0
#define USE_OPS 1
#define OPS_MODE 0
#define OPS_MIN_DISTANCE 0.8
#define OPS_MOVE_AFTER 50.0
#define OPS_RETRACT_DISTANCE 1.5
#define OPS_RETRACT_BACKLASH 0.0
#define USE_ADVANCE
#define BAUDRATE 250000
#define ENABLE_POWER_ON_STARTUP
#define POWER_INVERTING false
#define KILL_METHOD 1
#define GCODE_BUFFER_SIZE 2
#define ACK_WITH_LINENUMBER
#define WAITING_IDENTIFIER "wait"
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

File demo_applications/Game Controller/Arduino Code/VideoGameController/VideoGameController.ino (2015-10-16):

#include <CapacitiveSensor.h>

CapacitiveSensor   cs_2_3 = CapacitiveSensor(3, 2);
CapacitiveSensor   cs_4_5 = CapacitiveSensor(5, 4);
CapacitiveSensor   cs_6_7 = CapacitiveSensor(7, 6);
CapacitiveSensor   cs_8_9 = CapacitiveSensor(9, 8);
CapacitiveSensor   cs_10_11 = CapacitiveSensor(11, 10);
CapacitiveSensor   cs_12_13 = CapacitiveSensor(13, 12);

int previousButtonUpState = HIGH;   // for checking the state of a pushButton

void setup()
{
  cs_2_3.set_CS_AutocaL_Millis(0xFFFFFFFF);   // turn off autocalibrate on channel 1 - just as an example
  cs_4_5.set_CS_AutocaL_Millis(0xFFFFFFFF);
  cs_6_7.set_CS_AutocaL_Millis(0xFFFFFFFF);
  cs_8_9.set_CS_AutocaL_Millis(0xFFFFFFFF);   // turn off autocalibrate on channel 1 - just as an example
  cs_10_11.set_CS_AutocaL_Millis(0xFFFFFFFF);
  cs_12_13.set_CS_AutocaL_Millis(0xFFFFFFFF);
  Serial.begin(9600);
}


void loop() {
  // put your main code here, to run repeatedly:
  long start = millis();
  long total1 =  cs_2_3.capacitiveSensor(30);
  long total2 =  cs_4_5.capacitiveSensor(30);
  long total3 =  cs_6_7.capacitiveSensor(30);
  long total4 =  cs_8_9.capacitiveSensor(30);
  long total5 =  cs_10_11.capacitiveSensor(30);
  long total6 =  cs_12_13.capacitiveSensor(30);

Serial.println(total1);

  if ( (millis() % 100) != 0) {
    if (total1 > 5000)
      Serial.println('L');

    if (total2 > 5000)
      Serial.println('U');

    if (total3 > 5000)
      Serial.println('R');

    if (total4 > 5000)
      Serial.println('D');

    if (total5 > 5000)
      Serial.println('A');

    if (total6 > 5000)
      Serial.println('B');
  }
}

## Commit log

2014-04-19 Basic File System
    Added folder for firmware, extruder designs and applications.
2014-04-19 Initial batch of example applications
    Calibrations Shapes + Stylus + Congas + Game controller + Button Tests
    + Twitter button + Cup with measurement system
    [Congas.stl, Cup.stl, Design4.stl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]
2014-04-19 Revert "Initial batch of example applications"
    This reverts commit 700e4a533e63d6455600a55ef0c8e71041e48ee7.
    [Congas.stl, Cup.stl, Design4.stl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]
2014-04-23 Adding basic example applications
    [Game Controller(2).stl, Game Controller.stl, Glowing Rabbit(2).stl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]
2014-04-23 Added Code for video game controller example.
    [Game Controller(2).stl, Game Controller.stl, IPhone Stylus v3(2).stl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]
2014-04-23 Added capacitive musical interface file.
2014-04-23 Added syringe extruder design
    [Syringe support .stl]
2014-04-24 Conductive Paste Slicer Material Properties added
2014-04-24 Custom Rostock Max Firmware for the Rabbit Extruder. Based on Repetier firmware found on SeeMeCnc's repo for Rostock Max.
    [Configuration.h]
2014-09-05 extruder documentation
2015-10-16 Some more example files
    [Conductive glove(2).stl, Conductive glove.amf, Conductive glove.stl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]
2015-10-18 Added Rabbit Proto dual extruder CAD!
    [Extruder Assembly - Bottom.stl, Extruder Assembly - Middle.stl, Extruder Assembly - Top.stl]

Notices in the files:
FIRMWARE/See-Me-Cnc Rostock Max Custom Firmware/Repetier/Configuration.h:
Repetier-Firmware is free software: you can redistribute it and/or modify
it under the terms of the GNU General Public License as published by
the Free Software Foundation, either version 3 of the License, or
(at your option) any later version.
